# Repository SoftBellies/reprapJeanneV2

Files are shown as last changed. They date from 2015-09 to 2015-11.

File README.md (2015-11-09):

# reprapJeanneV2
Imprimante 3D grande taille

La [reprapJeanne](https://github.com/jeannedhack/reprapJeanne) 1 (projet non terminé) avait un problème de stabilité. On a trouvé des superbes profils alu, jetés aux encombrants par un commerçant du quartier qui pourraient corriger ce problème. Allez, nous sommes des ouf, on refait toute la conception!

Un nouveau dépôt git tout neuf qui reprendra pas mal d'éléments du précédent.
#Mécanique / structure

##Vue / schémas d'ensemble
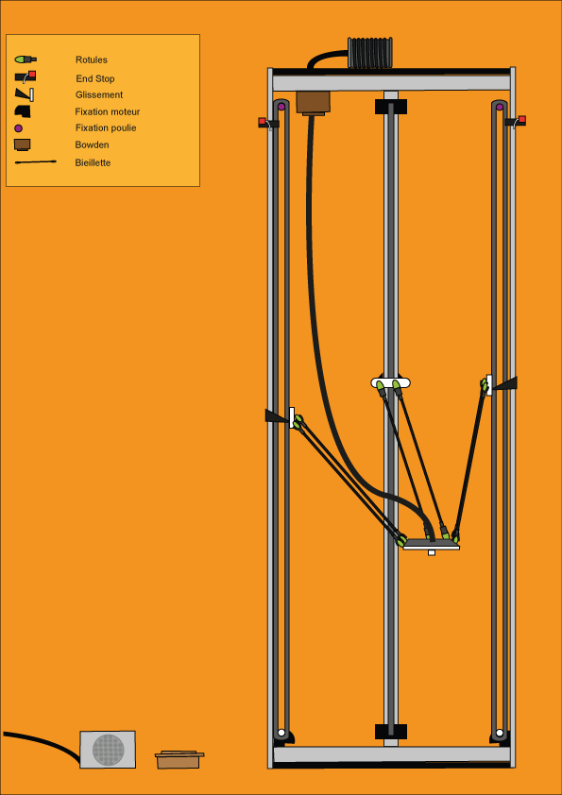
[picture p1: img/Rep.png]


##Détail des pièces

Nom de la pièce | à imprimer / acheter / fabriquer? | quantités | image | liens
-------------|-------------|---------|---------|----------------
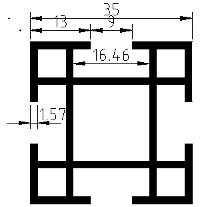
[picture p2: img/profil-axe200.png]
Axes aluminium 2m | Non, récupération | 3 |  | Le STL est dans le dossier STL de ce dépot et les fichiers de constructions dans le dossier DESSINS-DXF-OPENSCAD
liteaux (même profil que les axes) 646.5 mm arrondir par défaut lors de la découpe (peuvent être quelques millimetres plus petits mais peuvent pas être plus grand) | Non, récupération | 6 ou 9 |  |
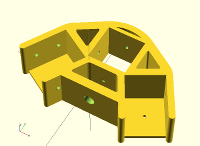
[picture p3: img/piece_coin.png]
Coins liteaux-axes | à imprimer | 6 ou 9 |  | 
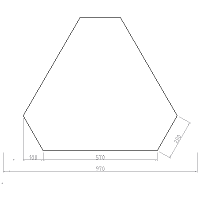
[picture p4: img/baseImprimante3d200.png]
Plateaux|Supports Bois à découper |2||Le DXF est dans le dépot.
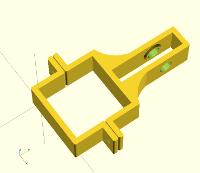
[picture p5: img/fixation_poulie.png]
Fixation poulie au bas des axes| à imprimer | 3|  | 
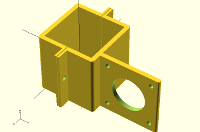
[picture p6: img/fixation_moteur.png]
Fixation moteurs en haut des axes| à imprimer | 3 |  |
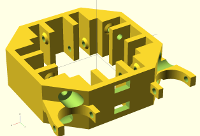
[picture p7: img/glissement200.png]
Glissements le long des axes | à imprimer | 3 |  |Le STL est dans le dossier STL de ce dépot et les fichiers de constructions dans le dossier DESSINS-DXF-OPENSCAD
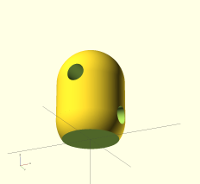
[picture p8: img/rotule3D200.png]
Rotules pour fixer la biellette aux glissements et à la plateforme | à imprimer | 12 | |Le STL est dans le dossier STL de ce dépot et les fichiers de constructions dans le dossier DESSINS-DXF-OPENSCAD
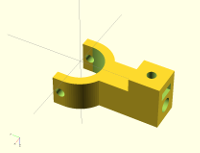
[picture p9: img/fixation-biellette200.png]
Pièce de liaison biellette / rotules| à imprimer | 12 | | Le STL est dans le dossier STL de ce dépôt et les fichiers de constructions dans le dossier DESSINS-DXF-OPENSCAD
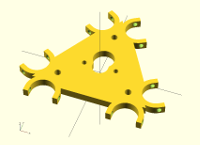
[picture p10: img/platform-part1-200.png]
Plate-forme d'extrusion partie 1 (adaptée à une buse J-Head- mini)| à imprimer |1 | | Le STL est dans le dossier STL de ce dépôt et les fichiers de constructions dans le dossier DESSINS-DXF-OPENSCAD
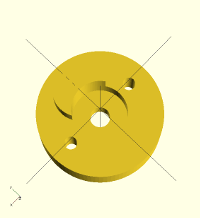
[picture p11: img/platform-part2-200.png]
Plateforme d'extrusion partie 2| à imprimer |1 | | Le STL est dans le dossier STL de ce dépôt et les fichiers de constructions dans le dossier DESSINS-DXF-OPENSCAD
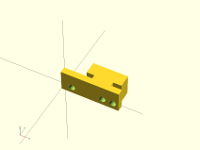
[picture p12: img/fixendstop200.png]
Fixation des fins de courses optiques sur les axes| à imprimer |3 | | Le STL est dans le dossier STL de ce dépôt et les fichiers de constructions dans le dossier DESSINS-DXF-OPENSCAD
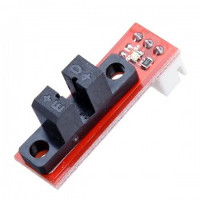
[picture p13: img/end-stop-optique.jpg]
fins de courses optiques| à ireprendre de l'ancienne imprimante |3 | |
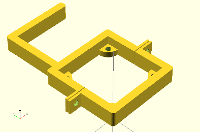
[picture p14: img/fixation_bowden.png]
Bowden|à imprimer partiellement | 1 |  | 
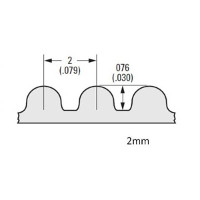
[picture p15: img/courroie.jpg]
Courroies GT2|à reprendre de l'ancienne imprimante | 3 * 4m | | l'image provient de [e-motiontech](http://www.reprap-france.com/produit/387-courroie-gt2-au-metre)
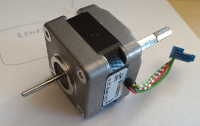
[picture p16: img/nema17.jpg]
Moteurs NEMA 17| à reprendre de l'ancienne imprimante| 4 | |Les moteurs achetés ont un petit défaut: seuls deux trous en façade sont filetés.
Roulements à bille 623 ZZ (pour les glissements)| à reprendre de l'ancienne imprimante| 24 | | 
Roulements à bille 624 ZZ (pour les retours de courroie)| à reprendre de l'ancienne imprimante| 3 | | 
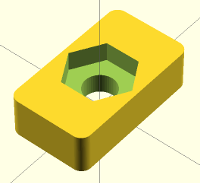
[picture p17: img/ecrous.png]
Truc pour bloquer des pièces dans les axes| à imprimer| a lot | |
#Électronique et firmware
Le classique dans le domaine des reprap Arduino Mega + Ramps + Polulus

##Firmware
Marlin https://github.com/MarlinFirmware/Marlin
Voir dans le dossier Firmware de ce dépôt pour les fichiers de configuration

##Octopi

# To do list à court terme
On utilise les "issues" de github pour répartir les tâches.
 
# Contribuer

Le plus simple est de venir nous rencontrer, le lundi soir, vers 20 h au hackerspace Jeannedhack (Rouen - France):  [https://www.jeannedhack.org/](https://www.jeannedhack.org/)

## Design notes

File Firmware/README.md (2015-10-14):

# reprapJeanneV2, Configuration du firmware

On utilisera Marlin https://github.com/MarlinFirmware/Marlin

Dans le dépot ReprapJeanneV, je ne mets que les fichiers de configuration.

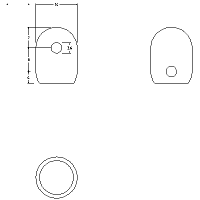
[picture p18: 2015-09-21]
img/rotule200.png

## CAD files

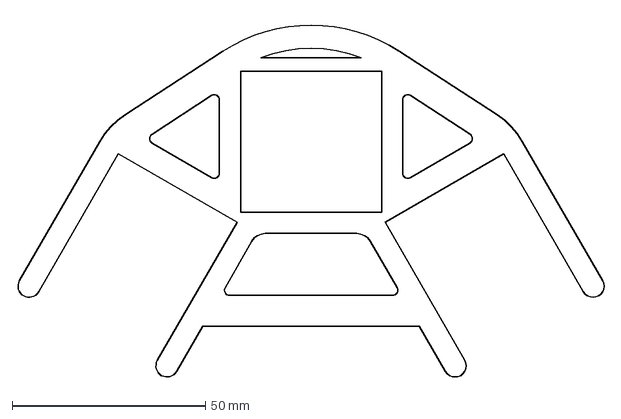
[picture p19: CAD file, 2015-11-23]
DESSINS-DXF-OPENSCAD/piece_coin.dxf
152.3 x 93.8 mm

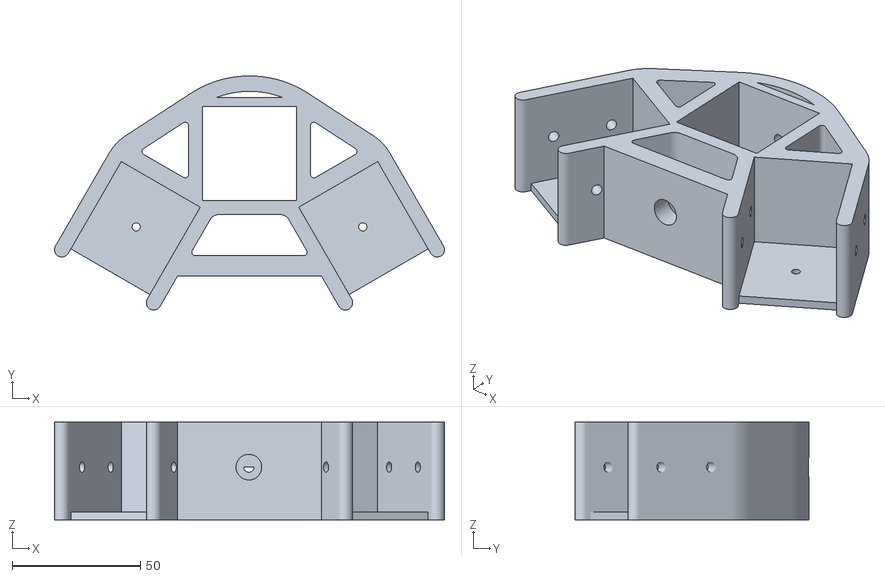
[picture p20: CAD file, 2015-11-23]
STL/piece_coin.stl
151.8 x 91.1 x 38.0

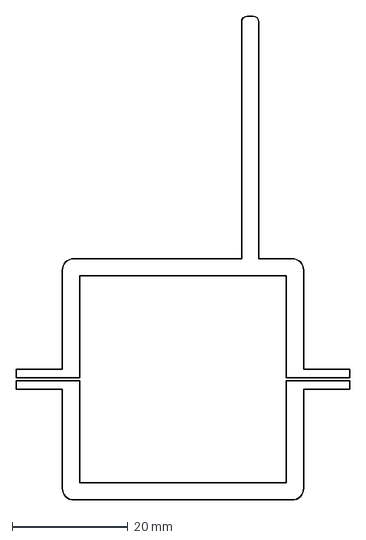
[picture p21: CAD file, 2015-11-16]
DESSINS-DXF-OPENSCAD/fixation_moteur.dxf
57.8 x 83.7 mm

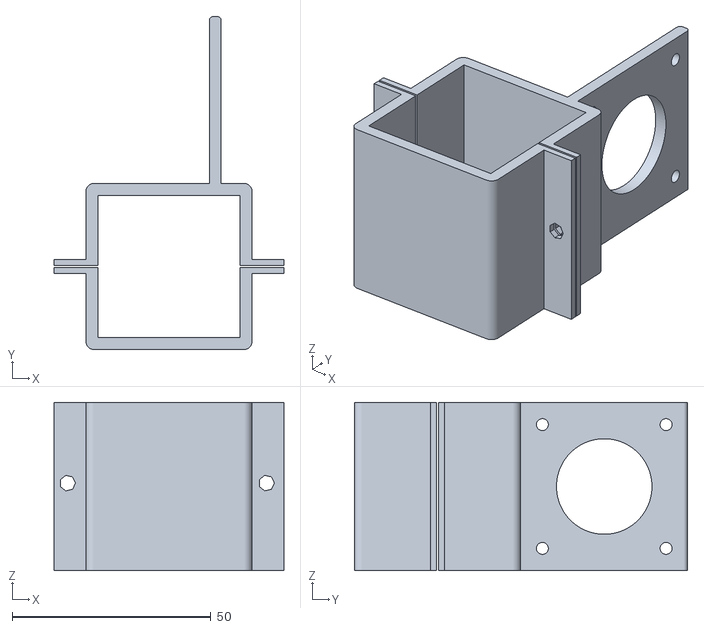
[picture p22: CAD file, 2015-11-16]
STL/fixation_moteur.stl
57.8 x 83.7 x 42.3

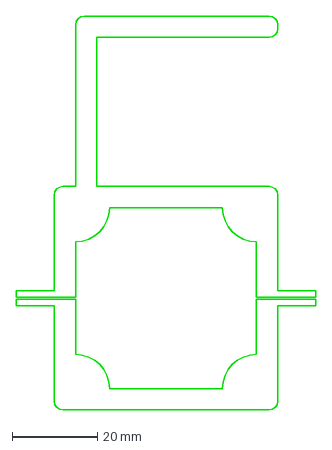
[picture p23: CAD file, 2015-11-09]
DESSINS-DXF-OPENSCAD/fixation_bowden.dxf
70.5 x 92.5 mm

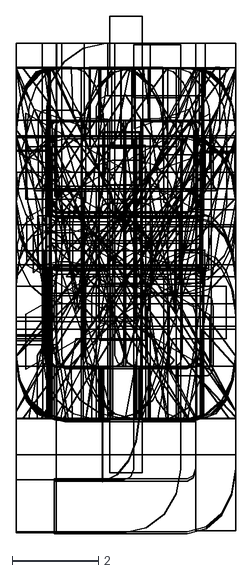
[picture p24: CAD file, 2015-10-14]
DESSINS-DXF-OPENSCAD/Writescad/orbitron.dxf
5.08 x 12.0

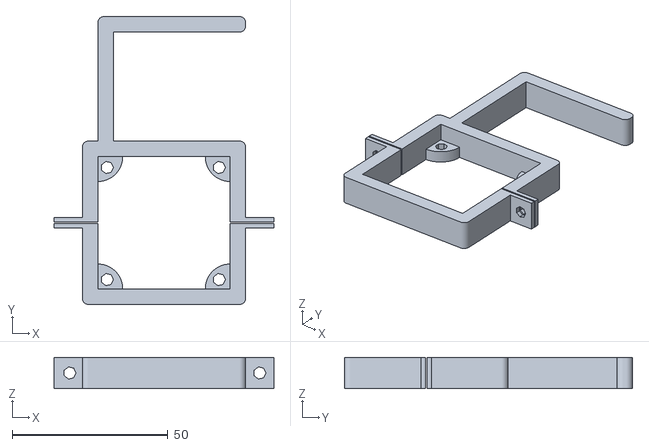
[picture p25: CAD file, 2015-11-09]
STL/fixation_bowden.stl
70.5 x 92.5 x 9.99

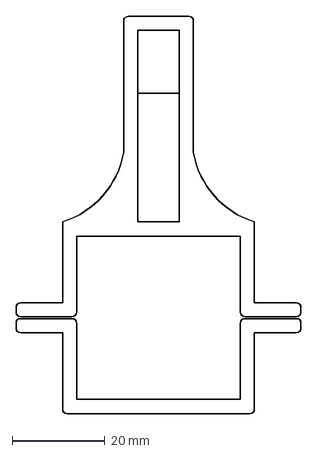
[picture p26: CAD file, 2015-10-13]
DESSINS-DXF-OPENSCAD/profil-axe.dxf
61.3 x 85.4 mm

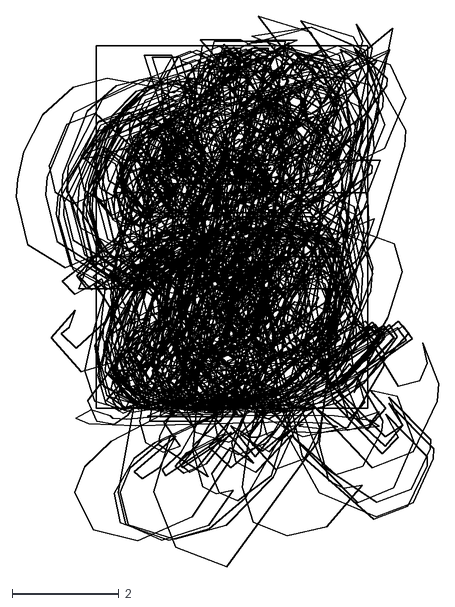
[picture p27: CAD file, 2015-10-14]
DESSINS-DXF-OPENSCAD/Writescad/BlackRose.dxf
7.90 x 10.3

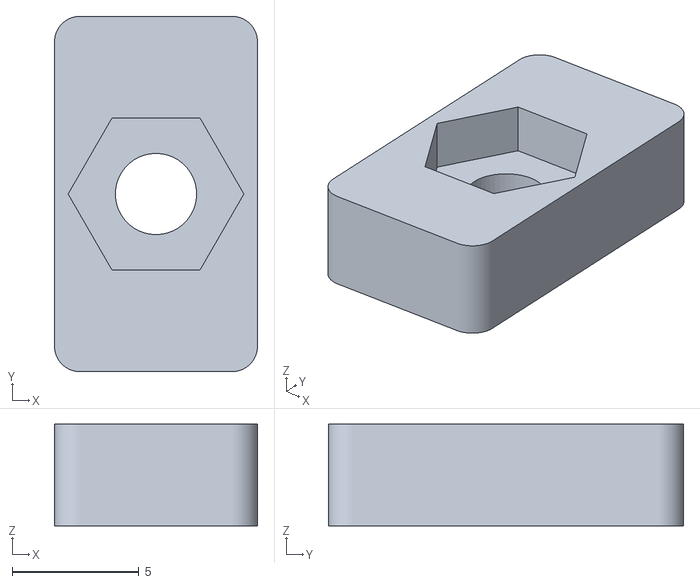
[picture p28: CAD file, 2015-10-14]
STL/ecrous.stl
8.00 x 14.0 x 4.00

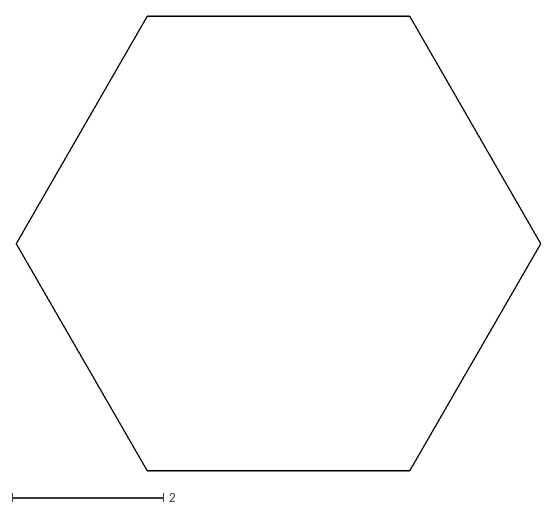
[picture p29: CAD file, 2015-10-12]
DESSINS-DXF-OPENSCAD/ecrou.dxf
6.93 x 6.00

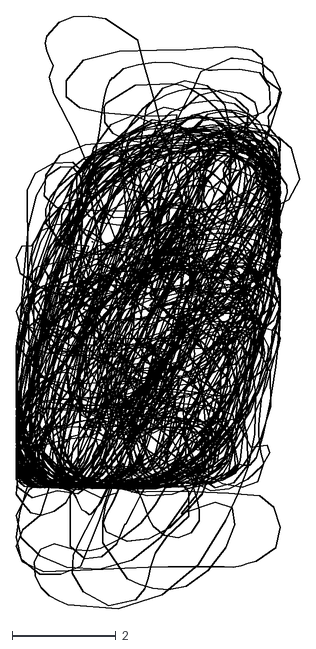
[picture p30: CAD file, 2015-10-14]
DESSINS-DXF-OPENSCAD/Writescad/knewave.dxf
5.46 x 11.4

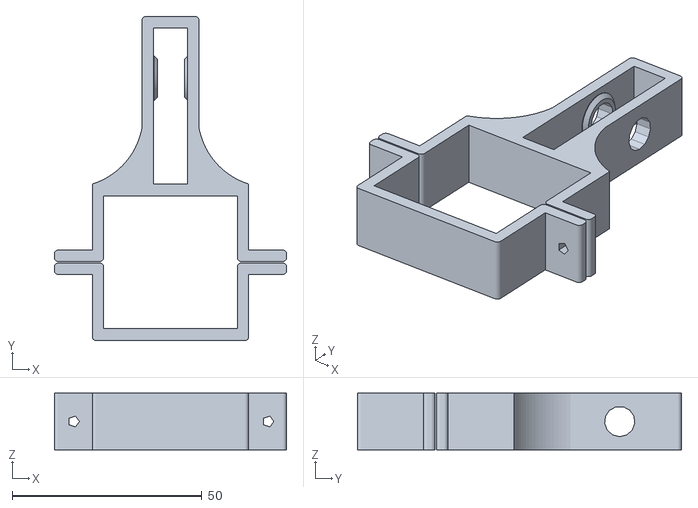
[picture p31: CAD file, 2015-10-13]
STL/fixationPoulie.stl
61.2 x 85.4 x 15.0

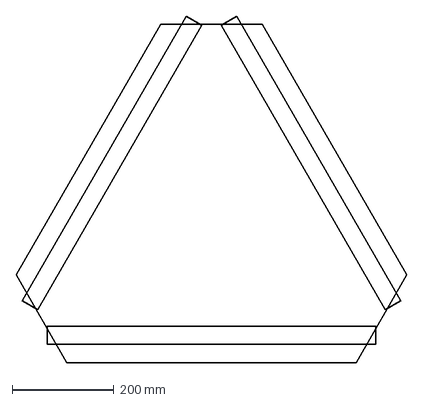
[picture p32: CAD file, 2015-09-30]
DESSINS-DXF-OPENSCAD/baseImprimante3d.dxf
770.0 x 681.7 mm

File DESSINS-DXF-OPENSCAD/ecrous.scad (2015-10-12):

difference(){

  	linear_extrude(height=4)
  		import (file="ecrou.dxf", layer="0", $fn=100);
	
	union(){
		translate([0,0,2])
			linear_extrude(height=2.4)
  				import (file="ecrou.dxf", layer="nut-fingerprint", $fn=100);
		translate([0,0,-0.1])
			cylinder(r=1.6,h=5,$fn=50);
	}	

}

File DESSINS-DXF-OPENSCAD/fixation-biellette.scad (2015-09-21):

/*
Projet ReprapJeanne

Fixations à chaque bouts des bielles
(les bielles sont des barres de cerf-volant: 
des cylindres de 4mm de diam et de 60 cm de long)

github: https://github.com/jeannedhack/reprapJeanneV2

hackerspace Jeanne d'hack https://www.jeannedhack.org
Gnieark https://blog-du-grouik.tinad.fr
& TranKILLoman   

License GNU-GPL 

*/

$fn=100;

fixationBiellette();

module fixationBiellette(){
  difference(){

	  union(){
		  difference(){
			  cylinder(r=10.5,h=10);
			  translate([-11,0,-0.001]) cube([22,11,11]);
		  }
		  translate([-10.5,-0.001,0]) cube([3,3.5,10]);
		  translate([7.5,-0.001,0]) cube([3,3.5,10]);
		  translate ([-5,-29,0])cube([10,19.7669,10]);
		  translate ([-5,-29,-4.599])cube([10,10,4.6]);
	  }
	  
	  union(){
		  translate([0,0,-0.001]) cylinder(r=7.5,h=15);
		  //trou de la biellette
		  translate([0,-29.01,5]) 
			  rotate([270,0,0]) 
				  cylinder(r=2.3,h=15);
		  //trou pour l'écrou (serrage)
		  translate([-2.85,-29.01,-1.6]) cube([5.7,10,2.7]);
		  //trou pour vis de serrage
		  translate([0,-24,-6]) cylinder(r=1.5,h=10);
		  //axe
		  translate([-11,1,5]) rotate([0,90,0]) cylinder(r=1.5,h=23);
	  }

  }
}

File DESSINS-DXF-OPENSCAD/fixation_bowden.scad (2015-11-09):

difference(){
	union(){
		linear_extrude(height=4)
		import (file="fixation_bowden.dxf", layer="0", $fn=100);
		translate([0,0,3.99])
		linear_extrude(height=6)
translate([0, 0, 3.99]) import (file="fixation_bowden.dxf", layer="1", $fn=100);
}
translate([3, 3, -5]) #cylinder(h=25, r=2);
translate([39, 3, -5]) #cylinder(h=25, r=2);
translate([3, 39, -5]) #cylinder(h=25, r=2);
translate([39, 39, -5]) #cylinder(h=25, r=2);
rotate([90, 0, 0]) translate([-9, 5, -32.5]) #cylinder(h=25, r=2);
rotate([90, 0, 0]) translate([52, 5, -32.5]) #cylinder(h=25, r=2);
}

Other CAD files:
DESSINS-DXF-OPENSCAD/Writescad/#braille.dxf
DESSINS-DXF-OPENSCAD/Writescad/Letters.dxf
STL/glissements.stl
DESSINS-DXF-OPENSCAD/platform.dxf
DESSINS-DXF-OPENSCAD/fixation_moteur.scad
DESSINS-DXF-OPENSCAD/Writescad/TestFont.scad
DESSINS-DXF-OPENSCAD/Writescad/TestSurfaceText.scad
DESSINS-DXF-OPENSCAD/Writescad/TestWrite.scad
DESSINS-DXF-OPENSCAD/Writescad/TestWriteCube.scad
DESSINS-DXF-OPENSCAD/Writescad/TestWriteCylinder.scad
DESSINS-DXF-OPENSCAD/Writescad/TestWriteSphere.scad
DESSINS-DXF-OPENSCAD/Writescad/Write-1.scad
DESSINS-DXF-OPENSCAD/Writescad/Write.scad
DESSINS-DXF-OPENSCAD/Writescad/braille.dxf
DESSINS-DXF-OPENSCAD/fixationPoulie.scad
DESSINS-DXF-OPENSCAD/fixendstop.scad
DESSINS-DXF-OPENSCAD/glissements.scad
DESSINS-DXF-OPENSCAD/piece_coin.scad
DESSINS-DXF-OPENSCAD/platform.scad
DESSINS-DXF-OPENSCAD/reprap.scad
DESSINS-DXF-OPENSCAD/rotule.dxf
DESSINS-DXF-OPENSCAD/rotule.scad
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

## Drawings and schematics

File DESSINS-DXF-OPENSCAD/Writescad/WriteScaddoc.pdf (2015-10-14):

p1

## WriteScad

By Harlan Martin
harlan@sutlog.com
January 2012

Version 2
Added support for future font selection (default is Letters.dxf) Added WriteCube module
Added Rotate for text (rotates on the plane of the text)
Added writesphere module

NOTE: These routines require openscad version 2011.12 or later

http://www.openscad.org/

-o-

## write()

Note about strings:
1... | The quote " symbol cannot be inserted into a string alone Either use \" or just the single quote' will show as "
2... | The \ is used for special text characters, so use the bar | to show the back slash \

Usage

Put the files (write.scad) and (letters.dfx) in the
| same directory as your project.

write("Hello World!",t=3,h=5,center=true);

(t=mm) (optional) The thickness of the letters in mm.
| The default is 1mm if not specified

(h=mm)(optional) The height of the letters in mm.
| The default is 4mm if not specified

(rotate=degrees) Rotates the text along the plane it is written on.

(center=boolean) (optional) Centers the text at default coordinates. Examples:

use <write.scad> // Dont forget to include this line

//example1: Uses all declarations..
| translate([20,15,0]) write("Example 1",t=4,h=5.75,center=true);

//example2: Quick and easy
| write("That was easy!",h=12);

//example3: move and rotate(front) (remember to translate..then rotate)
| translate([0,0,10]) rotate(90,[1,0,0]) // rotate around the x axis write("Rotate +X 90 (front)",t=2);

//example4: move and rotate(left side)
| translate([0,0,20]) rotate(90,[1,0,0]) // rotate around the x axis rotate(90,[0,-1,0]) // rotate around the y axis write("Rotate +X 90 and -Y 90 (left side)");

//example5: move and rotate(right side)
| translate([0,0,30]) rotate(90,[1,0,0]) // rotate around the x axis rotate(90,[0,1,0]) // rotate around the y axis write("Rotate +X 90 and +Y 90 (right side)");

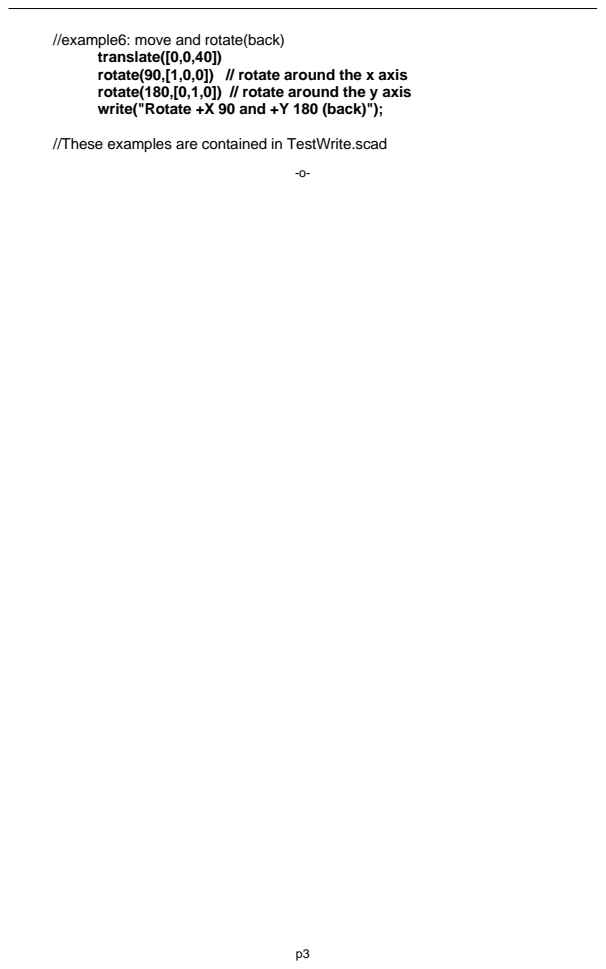
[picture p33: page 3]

//example6: move and rotate(back)

translate([0,0,40])
rotate(90,[1,0,0]) // rotate around the x axis
rotate(180,[0,1,0]) // rotate around the y axis
write("Rotate +X 90 and +Y 180 (back)");

//These examples are contained in TestWrite.scad

## writecube()

For these examples, assume we have the cube: use <write.scad>
translate([10,20,30])
cube(30,center=true);
text where and size
The values for text=, where= and size= are required, but if the values are entered in this order, then the commands are not required. These three examples produce the same results.

writecube(text="text", where=[10,20,30], size=[30,30,30]); or
writecube("text",[10,20,30], [30,30,30]);
or
writecube("text",[10,20,30],30);

text is written on the center front of a cube that is 30mm on all sides, and is centered at [10,20,30]

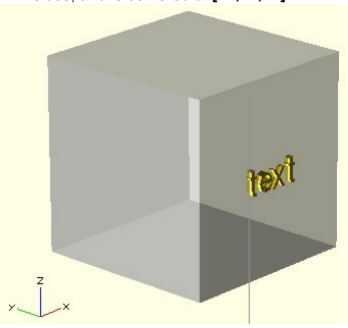
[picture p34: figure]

text="whatever text you want to write"
where= the center coordinates of the box
size = size of cube. If the cube is not square, use the format [xsize,ysize,zsize] If it is the same on all sides, just give the size ie. 30
face=
By default, writecube() will write on the front face of the box.
This assumes that x=left to right, y=front to back, z=bottom to top. To write on the other sides, use: face="top",face="bottom",face="back",face="front", face="left" or face="right"

writecube("Howdy!!",[10,20,30],30,face="left");

will print Howdy!! on the center left of the box.

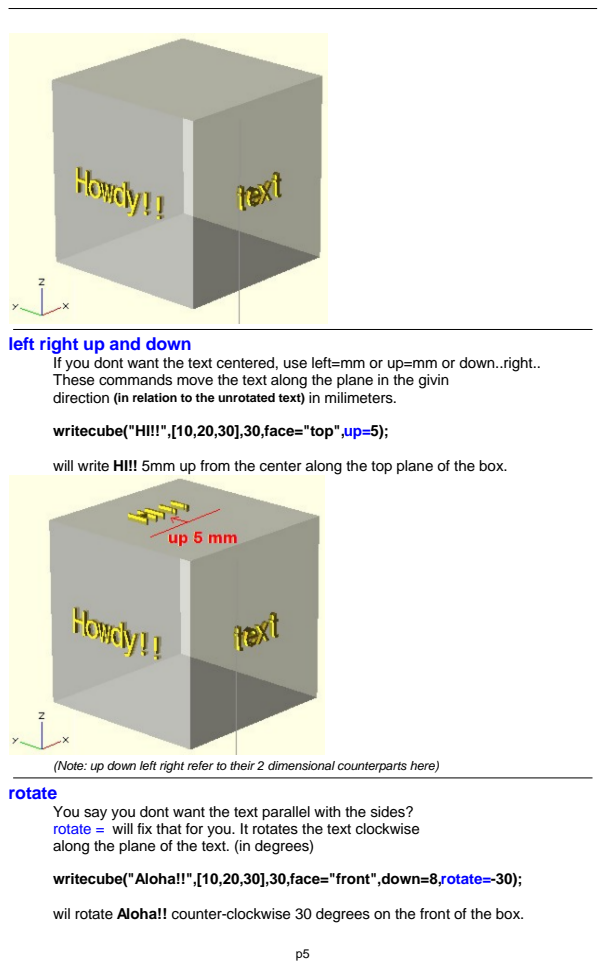
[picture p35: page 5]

left right up and down

If you dont want the text centered, use left=mm or up=mm or down..right..
These commands move the text along the plane in the givin
direction (in relation to the unrotated text) in milimeters.

writecube("HI!!",[10,20,30],30,face="top",up=5);

will write HI!! 5mm up from the center along the top plane of the box.

(Note: up down left right refer to their 2 dimensional counterparts here)
rotate

You say you dont want the text parallel with the sides?
rotate = will fix that for you. It rotates the text clockwise
along the plane of the text. (in degrees)

writecube("Aloha!!",[10,20,30],30,face="front",down=8,rotate=-30);

wil rotate Aloha!! counter-clockwise 30 degrees on the front of the box.

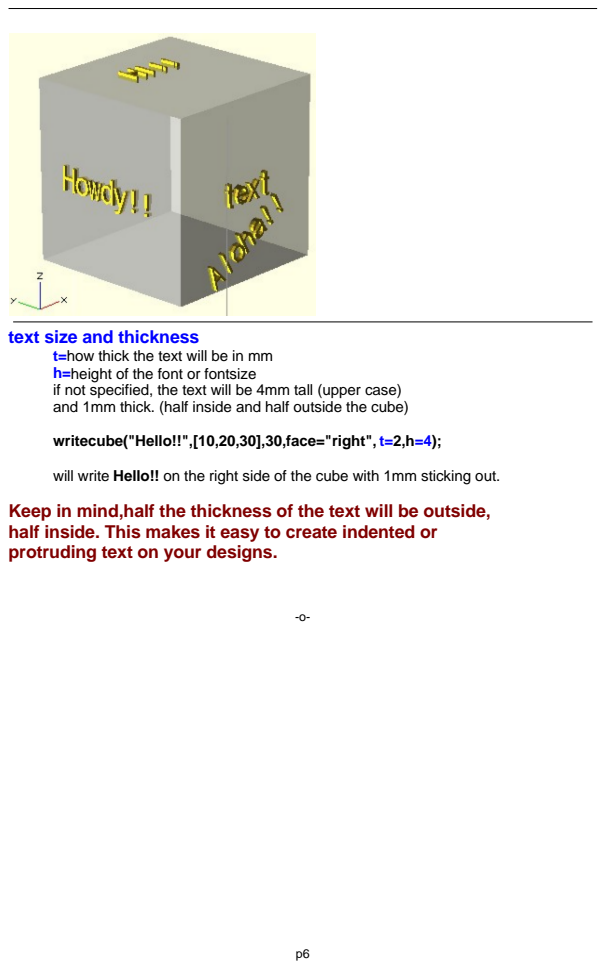
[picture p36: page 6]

text size and thickness

t=how thick the text will be in mm
h=height of the font or fontsize
if not specified, the text will be 4mm tall (upper case)
and 1mm thick. (half inside and half outside the cube)

writecube("Hello!!",[10,20,30],30,face="right", t=2,h=4);

will write Hello!! on the right side of the cube with 1mm sticking out.
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

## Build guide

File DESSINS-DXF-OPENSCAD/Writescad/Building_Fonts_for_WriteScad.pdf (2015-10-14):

p1

Harlan Martin

## Intro

Let me begin this by apologizing to everyone that uses InkScape.. These instructions are geared toward people like me that have never used it before. EVERYTHING in this help file is step by step. If there is a better way of doing it, let me know and I will revise the instructions.

Be forewarned... Making fonts is very tedious, but once you build a couple of letters, it's not very difficult. I tried to cover all the problems that I encountered while I was making fonts, but I might have missed a few. If so, contact me on Thingiverse (harlandmii) . Someone else might have the same problems.

Note: If you do take the time to build a font, PLEASE share it!!!!! I and anyone else that use it would be grateful :)

If you have problems, check the help section... I will try to keep it as updated as possible.

-o-

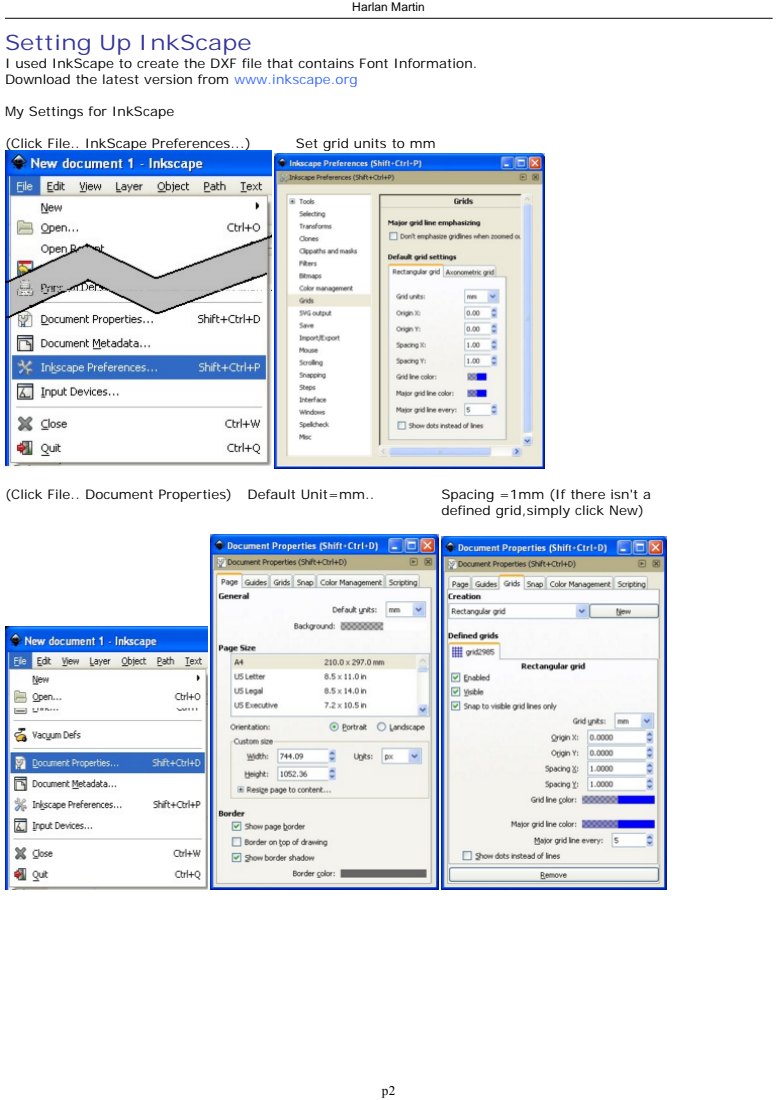
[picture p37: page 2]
(Click File.. InkScape Preferences...); Set grid units to mm; (Click File.. Document Properties); Default Unit=mm..; Spacing =1mm (If there isn't a

Setting Up InkScape
I used InkScape to create the DXF file that contains Font Information.
Download the latest version from www.inkscape.org

My Settings for InkScape

defined grid,simply click New)

To view the layers window.. (click Layer.. Layers)

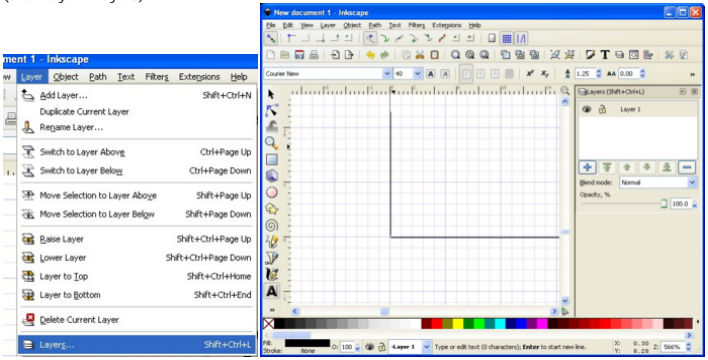
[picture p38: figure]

-o-

## Making a Guide

Click Create Text

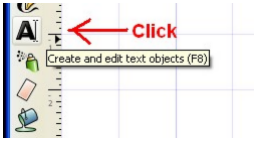
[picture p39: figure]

At the top of inkscape, Choose Desired Font and set font size to 40 (I also selected bold because courier is a thin font)

The first letter needs to be one of the larger letters, (Like capital M or W) so we can make a bounding guide to align the rest of the letters.

I am zoomed in pretty close here (1mm squares) Click in the bottom left of the page marker

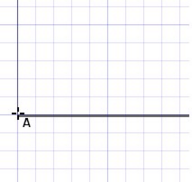
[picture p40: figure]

Type M

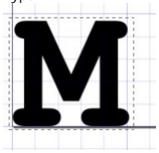
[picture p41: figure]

Use the Arrow (select and transform)
to align the letter to the left and bottom of the page marker.

Rename Layer 1 to the name of the letter

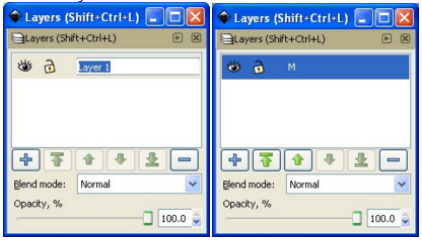
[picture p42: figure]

On the layers window, click the + to add a new layer. (Name it Border or something similar)
Use the Green Down Arrow to move it to the bottom of the list.

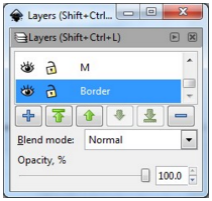
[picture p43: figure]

Make sure the Border layer is selected in the layers window. Click Create Rectangle and make a bounding box for the M
(I chose light pink)
All of the rest of the letters will be centered in this box.

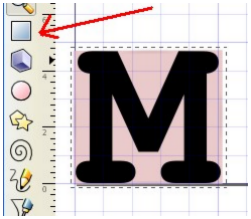
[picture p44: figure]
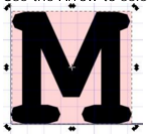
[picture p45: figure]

Use the Arrow to select the box

Click Path... Object to Path

Use Edit paths by nodes.
and select all four corners

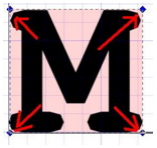
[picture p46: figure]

Click Make selected segments lines
(This process will be used on each letter to convert them to lines)

Lock the Border layer so it can't be accidentally changed.

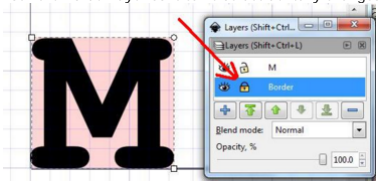
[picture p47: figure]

Choose the letter (M) Layer again..

Click the arrow (Select and transform) Click on the letter to select it

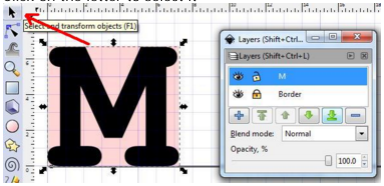
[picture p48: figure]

Click Path and Object to Path

Click Edit paths by nodes..
Then click on the letter to select it.

Drag a square around the letter to select all the nodes

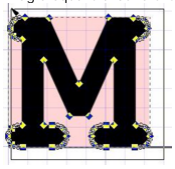
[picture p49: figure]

Click Make selected segments lines

If everything looks ok, we can go to the next letter. (If not, see the section on Making Letters Better)

-o-

## Making Letters

## Repeat the following steps for all letters and symbols

Click the + on the layers window to make a layer for
the next letter. (If its an A, name the layer A)
(lower case letter layers are named with a lower case letter and an underscore ie... the layer for lower case c would be c_ )
(layers are case sensitive)
(use the green arrows to put the layers in order if desired)

Close the eye on the M layer to hide it..
Then choose the A layer to edit

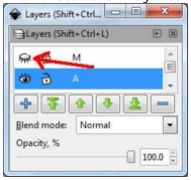
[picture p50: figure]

Choose create and edit text objects

Type the letter (A)

Use the Arrow to align it

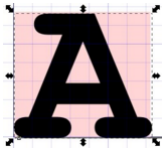
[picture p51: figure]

Click Path and Object to Path

Click edit paths by nodes
Click on the letter, then select all the nodes

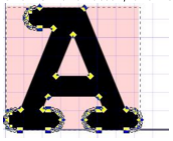
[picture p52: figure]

Click Make selected segments lines

### (That is the process for each letter)

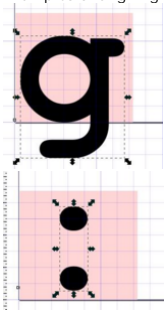
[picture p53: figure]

Examples of aligning letters

-o-

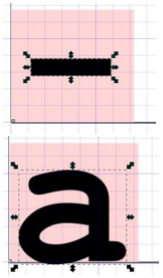
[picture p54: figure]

## Making Letters Better

Somtimes, when you click Path..Object to path, the image won't have enough points to make curved sides.

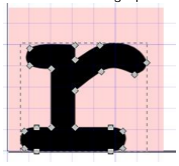
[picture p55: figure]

After you select all the nodes and click

Make Selected Segments Lines,
it becomes obvious.

If you don't like the looks of the letter, hold Ctrl and press Z to undo the change.

Click Edit paths by nodes
Select 2 or more nodes
(tip:click one node, then hold shift and click another) Then click Insert new nodes into selected segments.

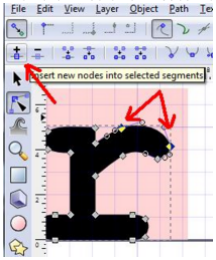
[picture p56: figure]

A new node will be on the curve.

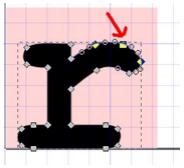
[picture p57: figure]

Repeat this process on each area that doesnt have enough
nodes to make the curves look smooth.

### NOTE: The more nodes a letter has, the slower it will draw in

OpenScad. The fewer, the better.

When your done adding nodes, select them all, and

click Make selected segments lines

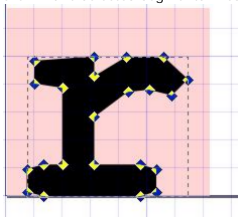
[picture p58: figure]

Move on to the next letter

-o-

## Saving the File

Be sure to save the SVG file each time.. Just click file.. Click save Name the file with the name of the font.

To use the font in OpenScad, we need to convert it to a DXF file.
Before saving the DXF, verify that all letters,boxes and shapes are converted to line segments. Otherwise, OpenScad won't be able to use it.

To make the DXF file:
Click File...
Click Save As...
Click the down arrow on save as type.. Choose Desktop Cutting Plotter(R13)(*.dxf)

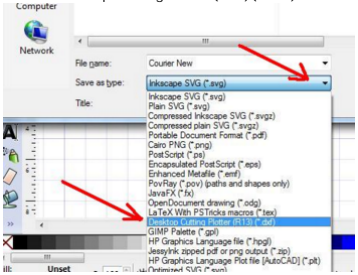
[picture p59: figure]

Click OK

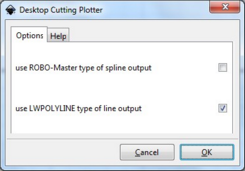
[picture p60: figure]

## Note: If you are testing a font as you create it, clear the cache on OpenScad the next time you update the Font... New letters won't appear until you do. (on OpenScad, click Design..click Flush Caches)

-o-

## HELP!!!

I will add this as soon as possible

-o-

## Testing While Making Fonts

-o-

## Font File Doesnt Work

-o-

## Some Letters Are Missing

-o-

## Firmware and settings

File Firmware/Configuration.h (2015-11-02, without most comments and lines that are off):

#define CONFIGURATION_H
#include "boards.h"
#define STRING_VERSION_CONFIG_H __DATE__ " " __TIME__ // build date and time
#define STRING_CONFIG_H_AUTHOR "Jeanne D'Hack" // Who made the changes.
#define SERIAL_PORT 0
#define BAUDRATE 115200
  #define MOTHERBOARD BOARD_RAMPS_13_EFF
#define EXTRUDERS 1
#define POWER_SUPPLY 1
#define DELTA
#define DELTA_SEGMENTS_PER_SECOND 200
#define DELTA_DIAGONAL_ROD 645.0 // mm
#define DELTA_SMOOTH_ROD_OFFSET 378.35 // mm
#define DELTA_EFFECTOR_OFFSET 27.5 // mm
#define DELTA_CARRIAGE_OFFSET 18.35 // mm
#define DELTA_RADIUS (DELTA_SMOOTH_ROD_OFFSET-DELTA_EFFECTOR_OFFSET-DELTA_CARRIAGE_OFFSET)
#define TEMP_SENSOR_0 1
#define TEMP_SENSOR_1 1
#define TEMP_SENSOR_2 0
#define TEMP_SENSOR_BED 0
#define MAX_REDUNDANT_TEMP_SENSOR_DIFF 10
#define TEMP_RESIDENCY_TIME 10  // (seconds)
#define TEMP_HYSTERESIS 3       // (degC) range of +/- temperatures considered "close" to the target one
#define TEMP_WINDOW     1       // (degC) Window around target to start the residency timer x degC early.
#define HEATER_0_MINTEMP 5
#define HEATER_1_MINTEMP 5
#define HEATER_2_MINTEMP 5
#define BED_MINTEMP 5
#define HEATER_0_MAXTEMP 275
#define HEATER_1_MAXTEMP 275
#define HEATER_2_MAXTEMP 275
#define BED_MAXTEMP 150
#define PIDTEMP
#define BANG_MAX 255 // limits current to nozzle while in bang-bang mode; 255=full current
#define PID_MAX 255 // limits current to nozzle while PID is active (see PID_FUNCTIONAL_RANGE below); 255=full current
  #define PID_FUNCTIONAL_RANGE 10 // If the temperature difference between the target temperature and the actual temperature
  #define PID_INTEGRAL_DRIVE_MAX 255  //limit for the integral term
  #define K1 0.95 //smoothing factor within the PID
  #define PID_dT ((OVERSAMPLENR * 10.0)/(F_CPU / 64.0 / 256.0)) //sampling period of the temperature routine
    #define  DEFAULT_Kp 22.2
    #define  DEFAULT_Ki 1.08
    #define  DEFAULT_Kd 114
#define MAX_BED_POWER 255 // limits duty cycle to bed; 255=full current
#define PREVENT_DANGEROUS_EXTRUDE
#define PREVENT_LENGTHY_EXTRUDE
#define EXTRUDE_MINTEMP 170
#define EXTRUDE_MAXLENGTH (X_MAX_LENGTH+Y_MAX_LENGTH) //prevent extrusion of very large distances.
#define ENDSTOPPULLUPS // Comment this out (using // at the start of the line) to disable the endstop pullup resistors
  #define ENDSTOPPULLUP_XMAX
  #define ENDSTOPPULLUP_YMAX
  #define ENDSTOPPULLUP_ZMAX
  #define ENDSTOPPULLUP_XMIN
  #define ENDSTOPPULLUP_YMIN
  #define ENDSTOPPULLUP_ZMIN
const bool X_MIN_ENDSTOP_INVERTING = true; // set to true to invert the logic of the endstop.
const bool Y_MIN_ENDSTOP_INVERTING = true; // set to true to invert the logic of the endstop.
const bool Z_MIN_ENDSTOP_INVERTING = true; // set to true to invert the logic of the endstop.
const bool X_MAX_ENDSTOP_INVERTING = true; // set to true to invert the logic of the endstop.
const bool Y_MAX_ENDSTOP_INVERTING = true; // set to true to invert the logic of the endstop.
const bool Z_MAX_ENDSTOP_INVERTING = true; // set to true to invert the logic of the endstop.
#define DISABLE_MIN_ENDSTOPS
#if defined(COREXY) && !defined(DISABLE_MAX_ENDSTOPS)
  #define DISABLE_MAX_ENDSTOPS
#endif
#define X_ENABLE_ON 0
#define Y_ENABLE_ON 0
#define Z_ENABLE_ON 0
#define E_ENABLE_ON 0 // For all extruders
#define DISABLE_X false
#define DISABLE_Y false
#define DISABLE_Z false
#define DISABLE_E false // For all extruders
#define DISABLE_INACTIVE_EXTRUDER true //disable only inactive extruders and keep active extruder enabled
#define INVERT_X_DIR false // DELTA does not invert
#define INVERT_Y_DIR false
#define INVERT_Z_DIR false
#define INVERT_E0_DIR false   // for direct drive extruder v9 set to true, for geared extruder set to false
#define INVERT_E1_DIR false    // for direct drive extruder v9 set to true, for geared extruder set to false
#define INVERT_E2_DIR false   // for direct drive extruder v9 set to true, for geared extruder set to false
#define X_HOME_DIR 1
#define Y_HOME_DIR 1
#define Z_HOME_DIR 1
#define min_software_endstops true // If true, axis won't move to coordinates less than HOME_POS.
#define max_software_endstops true  // If true, axis won't move to coordinates greater than the defined lengths below.
#define X_MAX_POS 90
#define X_MIN_POS -90
#define Y_MAX_POS 90
#define Y_MIN_POS -90
#define Z_MAX_POS MANUAL_Z_HOME_POS
#define Z_MIN_POS 0
#define X_MAX_LENGTH (X_MAX_POS - X_MIN_POS)
#define Y_MAX_LENGTH (Y_MAX_POS - Y_MIN_POS)
#define Z_MAX_LENGTH (Z_MAX_POS - Z_MIN_POS)
#define MANUAL_HOME_POSITIONS  // MANUAL_*_HOME_POS below will be used
#define MANUAL_X_HOME_POS 0
#define MANUAL_Y_HOME_POS 0
#define MANUAL_Z_HOME_POS 250 // For delta: Distance between nozzle and print surface after homing.
#define NUM_AXIS 4 // The axis order in all axis related arrays is X, Y, Z, E
#define HOMING_FEEDRATE {200*60, 200*60, 200*60, 0}  // set the homing speeds (mm/min)
#define DEFAULT_AXIS_STEPS_PER_UNIT   {80, 80, 80, 760*1.1}  // default steps per unit for Kossel (GT2, 20 tooth)
#define DEFAULT_MAX_FEEDRATE          {500, 500, 500, 25}    // (mm/sec)
#define DEFAULT_MAX_ACCELERATION      {9000,9000,9000,10000}    // X, Y, Z, E maximum start speed for accelerated moves. E default values are good for skeinforge 40+, for older versions raise them a lot.
#define DEFAULT_ACCELERATION          3000    // X, Y, Z and E max acceleration in mm/s^2 for printing moves
#define DEFAULT_RETRACT_ACCELERATION  3000   // X, Y, Z and E max acceleration in mm/s^2 for retracts
#define DEFAULT_XYJERK                20.0    // (mm/sec)
#define DEFAULT_ZJERK                 20.0    // (mm/sec) Must be same as XY for delta
#define DEFAULT_EJERK                 5.0    // (mm/sec)
#define CUSTOM_M_CODES
  #define CUSTOM_M_CODE_SET_Z_PROBE_OFFSET 851
  #define Z_PROBE_OFFSET_RANGE_MIN -15
  #define Z_PROBE_OFFSET_RANGE_MAX -5
#define PLA_PREHEAT_HOTEND_TEMP 180
#define PLA_PREHEAT_HPB_TEMP 70
#define PLA_PREHEAT_FAN_SPEED 255   // Insert Value between 0 and 255
#define ABS_PREHEAT_HOTEND_TEMP 240
#define ABS_PREHEAT_HPB_TEMP 100
#define ABS_PREHEAT_FAN_SPEED 255   // Insert Value between 0 and 255
#define SOFT_PWM_SCALE 0
#define FILAMENT_SENSOR_EXTRUDER_NUM  0  //The number of the extruder that has the filament sensor (0,1,2)
#define MEASUREMENT_DELAY_CM      14  //measurement delay in cm.  This is the distance from filament sensor to middle of barrel
#define DEFAULT_NOMINAL_FILAMENT_DIA  3.0  //Enter the diameter (in mm) of the filament generally used (3.0 mm or 1.75 mm) - this is then used in the slicer software.  Used for sensor reading validation
#define MEASURED_UPPER_LIMIT          3.30  //upper limit factor used for sensor reading validation in mm
#define MEASURED_LOWER_LIMIT          1.90  //lower limit factor for sensor reading validation in mm
#define MAX_MEASUREMENT_DELAY     20  //delay buffer size in bytes (1 byte = 1cm)- limits maximum measurement delay allowable (must be larger than MEASUREMENT_DELAY_CM  and lower number saves RAM)
#define DEFAULT_MEASURED_FILAMENT_DIA  DEFAULT_NOMINAL_FILAMENT_DIA  //set measured to nominal initially
#include "Configuration_adv.h"
#include "thermistortables.h"

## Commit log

2015-09-07 profil axe
    [profil-axe.dxf, reprap.scad]
2015-09-18 trous élargis pour les têtes des vis
    [glissements.scad, glissements.stl]
2015-09-18 glissements: ajout de la forme pour fixer les rotules
    [glissements.scad, glissements.stl, profil-axe.dxf]
2015-09-19 Dessin du moteur nema 17
    [profil-axe.dxf]
2015-09-21 fixation bielette
    [fixation-biellette.scad, fixation-biellette.stl, glissements.scad]
2015-09-21 Plate forme de support de la tete d'extrusion
    [platform-part1.stl, platform-part2.stl, platform.dxf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]
2015-09-21 Ajout de la première version de la fixation du end-stop optique
    [fixendstop.scad]
2015-09-21 openscad has a problem, I almost lost my work...
    [fixendstop.scad]
2015-09-22 ajout de la fixation des fins de courses dessinées par Moebius dans le Readme
    [fixendstop.scad, fixendstop.stl]
2015-09-29 description des pièces dans le readme
2015-09-30 dessin de structure
    [baseImprimante3d.dxf, structure.scad]
2015-09-30 pieces dans des modules openscad afin de pouvoir les utiliser plus facilement dans d'autres fichiers
    [fixendstop.scad, glissements.scad, reprap.scad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]
2015-09-30 trous pour fixation courroie sur le glissement
    [glissements.scad, glissements.stl, profil-axe.dxf]
2015-10-05 fixation Poulie
    [fixationPoulie.scad]
2015-10-05 fixation moteur de faite xd
    [fixation_moteur.dxf, fixation_moteur.scad, fixation_moteur.stl]
2015-10-08 dessin d'ensemble reprap.scad, intégration fixation moteur sur un des axes
    [fixation_moteur.scad, reprap.scad]
2015-10-08 dessin d'ensemble: ajout des deux autres fixations moteur
    [reprap.scad]
2015-10-08 ajout fixations poulies et glissements au dessin d'ensemble
    [fixationPoulie.scad, reprap.scad]
2015-10-09 Ajout d'un rebord pour caler le roulement à bille
    [fixationPoulie.scad, fixationPoulie.stl]
2015-10-12 correction marges, et ajout d'arrondis sur la fixation moteurs
    [fixation_moteur.dxf, fixation_moteur.stl]
2015-10-12 pièce du coin
    [piece_coin.dxf, piece_coin.scad]
2015-10-13 Rapprochement de a pièce du 0,0 pour éviter le bug openscad
    [piece_coin.dxf, piece_coin.scad]
2015-10-13 Reste trous pour vis à ajouter
    [piece_coin.dxf, piece_coin.scad]
2015-10-13 pièce du coin enfin finite
    [piece_coin.dxf, piece_coin.scad, piece_coin.stl]
2015-10-13 Oups, j'avais écrasé les modifs de Timoth lors d'un merge. sorry, retour des bons fichiers
    [fixationPoulie.scad, fixationPoulie.stl, profil-axe.dxf]
2015-10-13 arrondis et renforcements de la pièce
    [piece_coin.dxf, piece_coin.scad, piece_coin.stl]
2015-10-14 ajout des fichiers de conf du firmware
    [Configuration.h, Configuration_adv.h]
2015-10-14 inscription plus grosse
    [ecrous.stl, piece_coin.scad, piece_coin.stl]
2015-10-21 longeur des liteaux
2015-10-26 fichier modifié
    [Configuration.h]
2015-11-09 mise a jour fixation bowden
    [fixation_bowden.dxf, fixation_bowden.scad, fixation_bowden.stl]
2015-11-12 Pièce plus épaisse (+2mm) Trous prévus pour vis 4mm de diam déplacement et changement des inscriptions
    modifié : DESSINS-DXF-OPENSCAD/piece_coin.dxf
    modifié : DESSINS-DXF-OPENSCAD/piece_coin.scad
    modifié : STL/piece_coin.stl
    modifié : img/piece_coin.png
    [piece_coin.dxf, piece_coin.scad, piece_coin.stl]
2015-11-16 modifications fixation moteur
    [fixation_moteur.dxf, fixation_moteur.scad, fixation_moteur.stl]
2015-11-23 allez hop le stl et le png maintenant
    [piece_coin.stl]
2015-11-23 le png à la bonne taille
